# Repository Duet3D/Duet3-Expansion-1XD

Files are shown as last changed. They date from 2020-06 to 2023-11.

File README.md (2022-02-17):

# Duet 3 Expansion 1XD
Hardware information for the Duet 3 Expansion 1XD. This is a CAN-FD connected expansion board for the [Duet 3 Mainboard](https://www.duet3d.com/Duet3Mainboard6HC) and [Duet 3 Mini 5+](https://www.duet3d.com/Duet3Mini5plus) that allows connection for a single external stepper driver and associated peripherals.

Image of Duet 3 Expansion 1XD

Product page is here: https://www.duet3d.com/Duet3Expansion1XD 

Documentation is here: https://docs.duet3d.com/Duet3D_hardware/Duet_3_family/Duet_3_Expansion_1XD

As always please discuss this on the Duet3d forum: https://forum.duet3d.com/

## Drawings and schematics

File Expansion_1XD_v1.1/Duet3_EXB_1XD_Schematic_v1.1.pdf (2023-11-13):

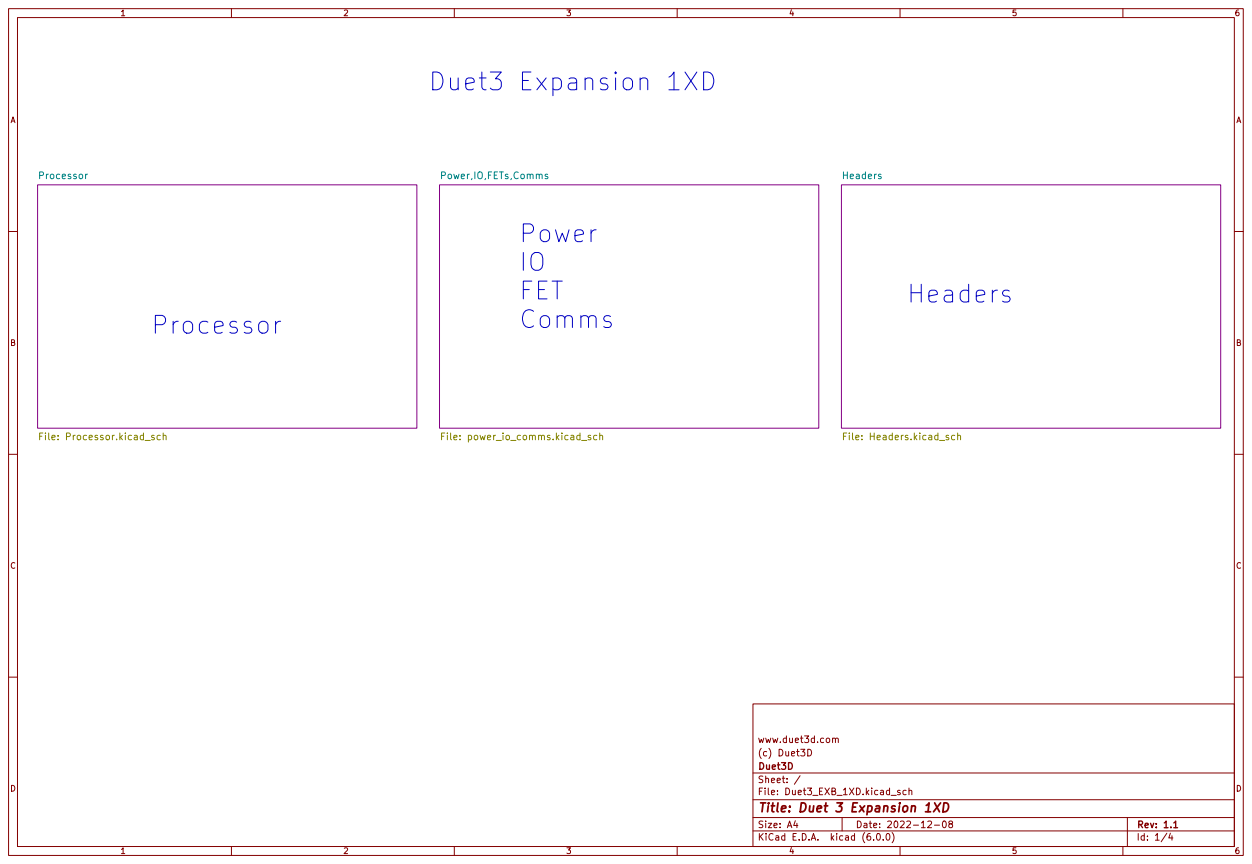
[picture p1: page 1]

Headers File: Headers.kicad_sch Processor File: Processor.kicad_sch

Id: 1/4 Title: Duet 3 Expansion 1XD

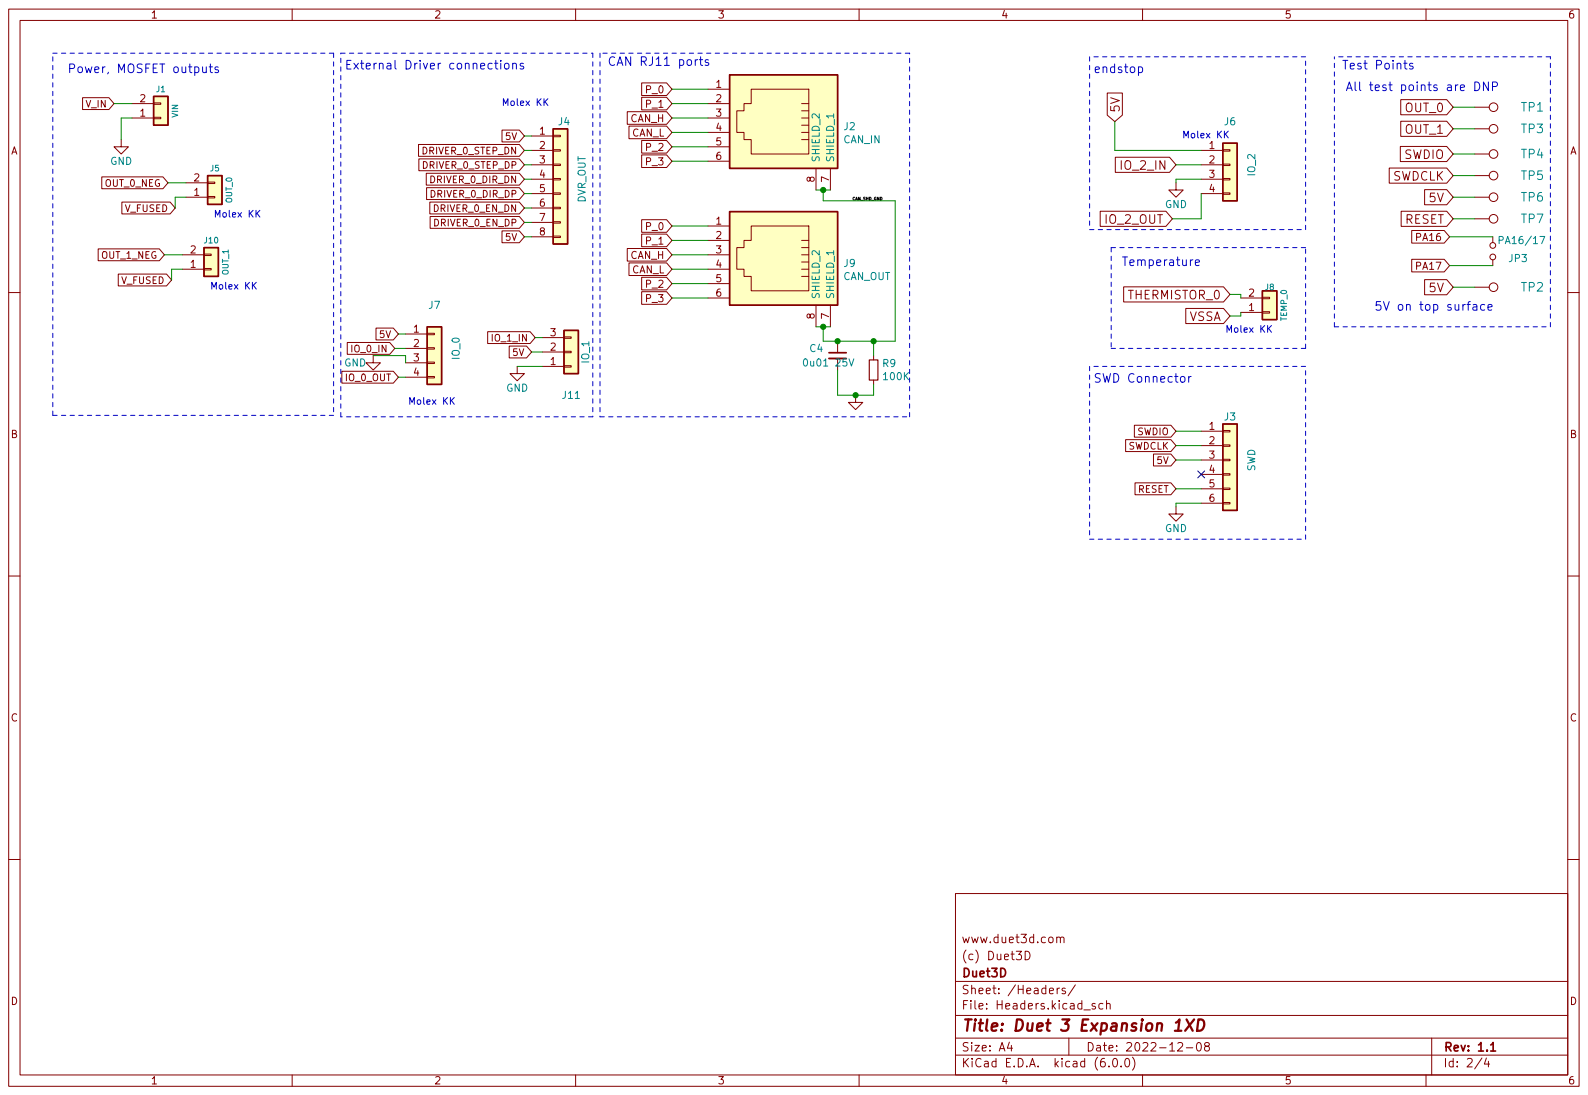
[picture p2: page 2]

All test points are DNP

www.duet3d.com
(c) Duet3D
File: Headers.kicad_sch Sheet: /Headers/ Duet3D

Id: 2/4 Title: Duet 3 Expansion 1XD

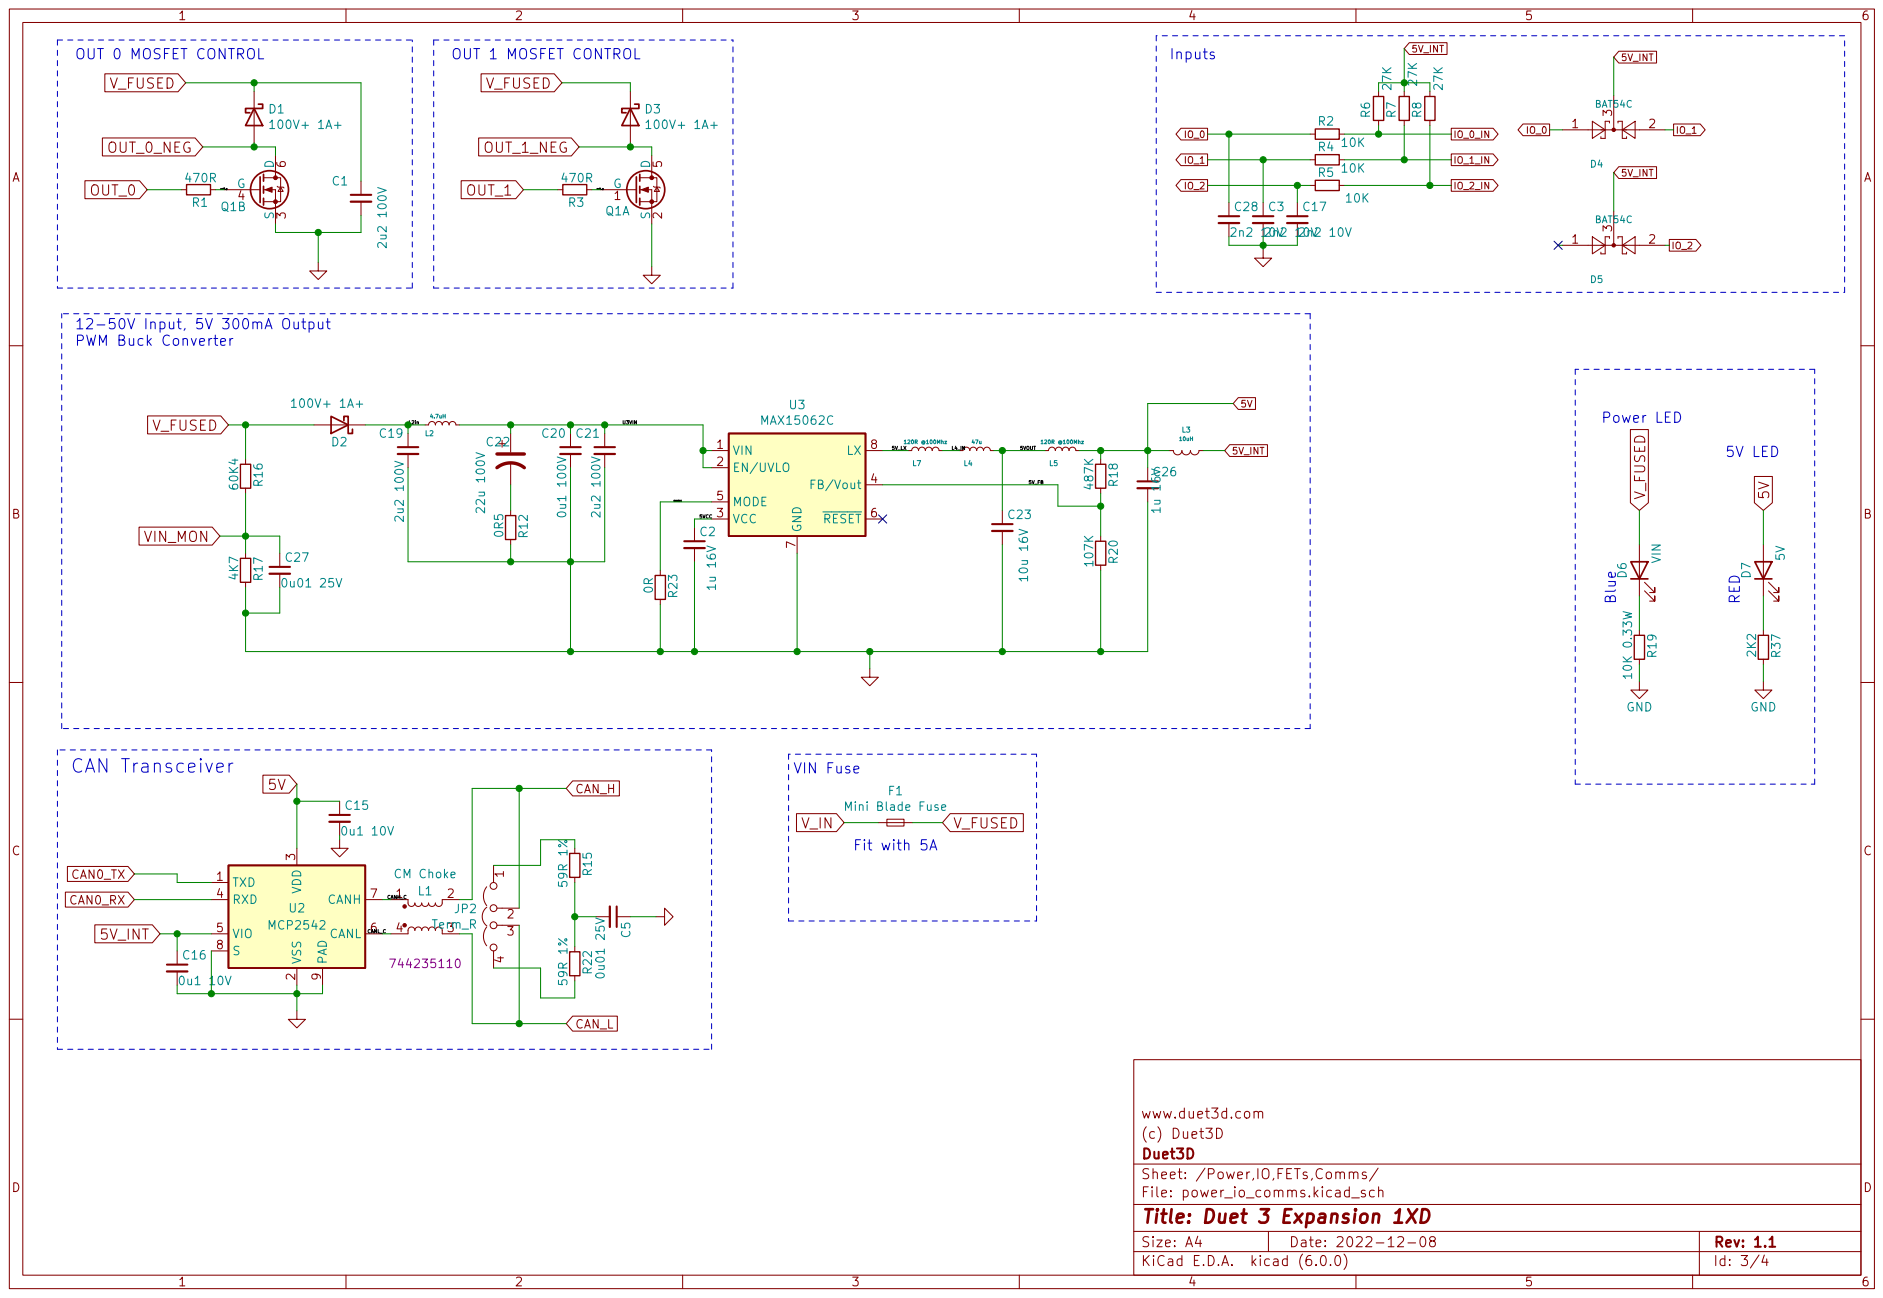
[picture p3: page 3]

Inputs VIN Fuse OUT 0 MOSFET CONTROL
V_FUSED

Fit with 5A CAN Transceiver

3 RXD 4 VIO 5 CANL 6 CANH 7 S

www.duet3d.com
(c) Duet3D
Sheet: /Power,IO,FETs,Comms/ Duet3D

File: power_io_comms.kicad_sch
Id: 3/4 Title: Duet 3 Expansion 1XD

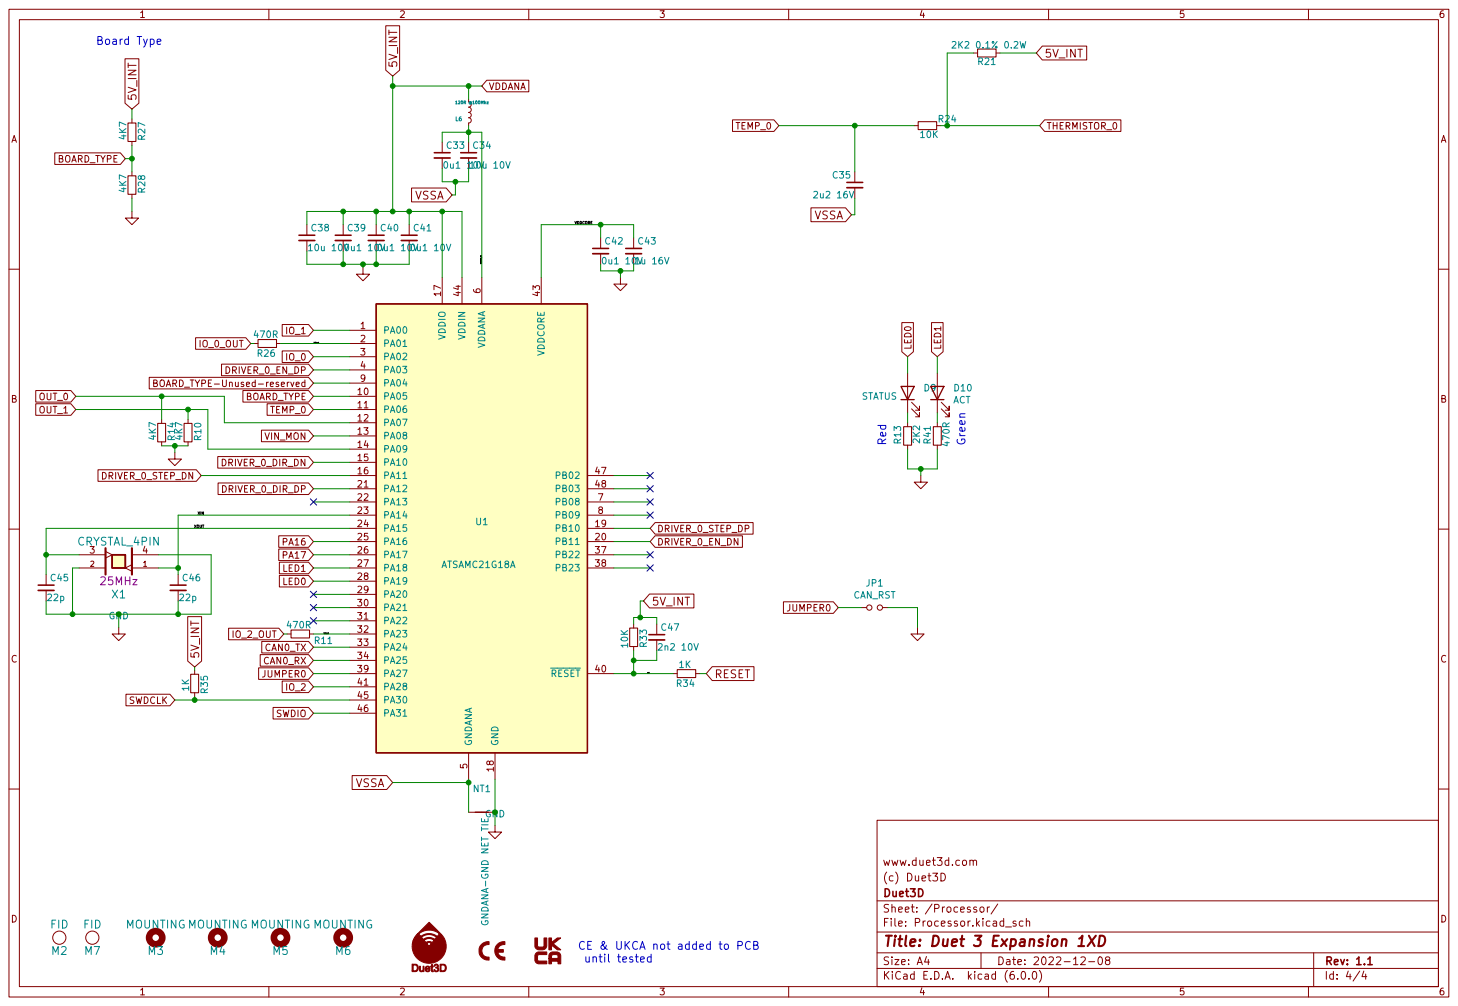
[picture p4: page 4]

www.duet3d.com
(c) Duet3D
File: Processor.kicad_sch Sheet: /Processor/ Duet3D

CE & UKCA not added to PCB
until tested

Id: 4/4 Title: Duet 3 Expansion 1XD

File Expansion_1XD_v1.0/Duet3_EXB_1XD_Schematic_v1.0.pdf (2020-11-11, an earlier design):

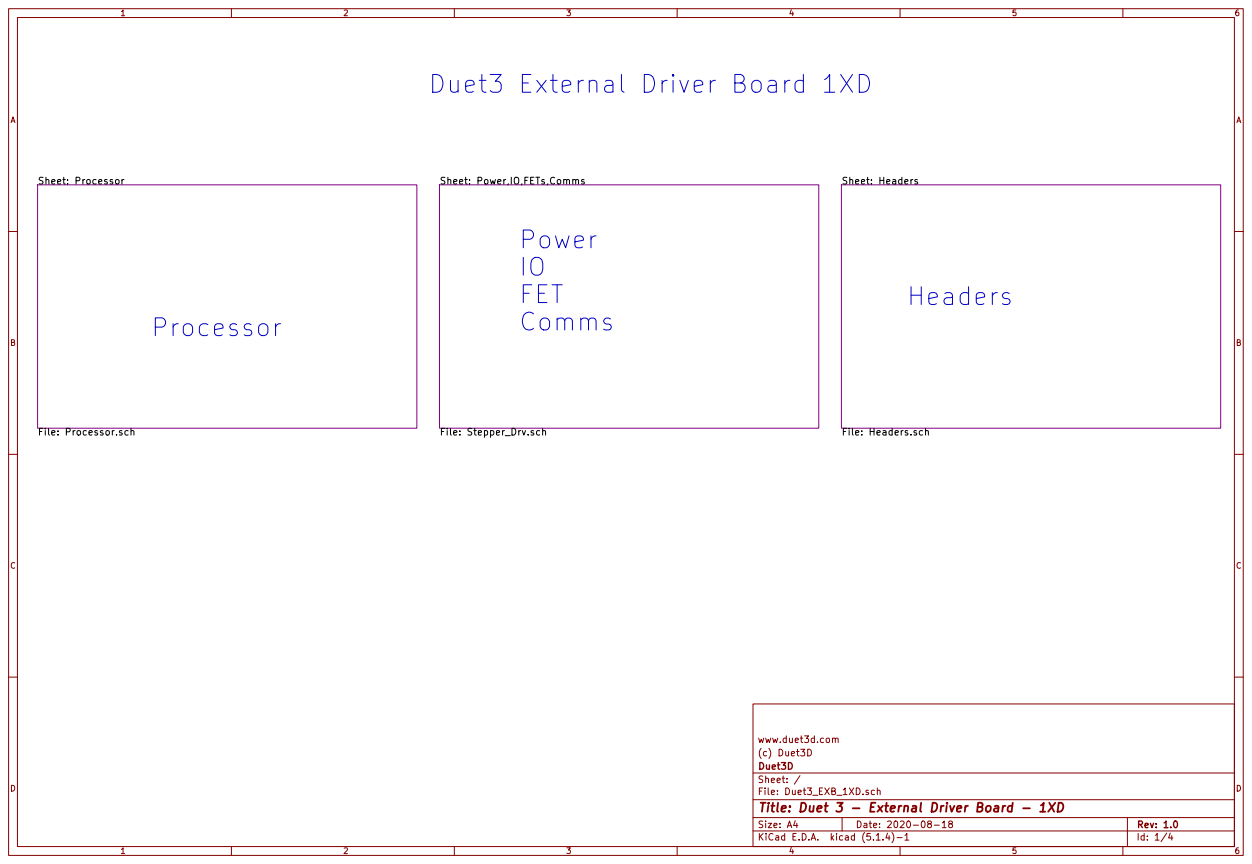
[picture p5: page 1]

Id: 1/4 Title: Duet 3 - External Driver Board - 1XD

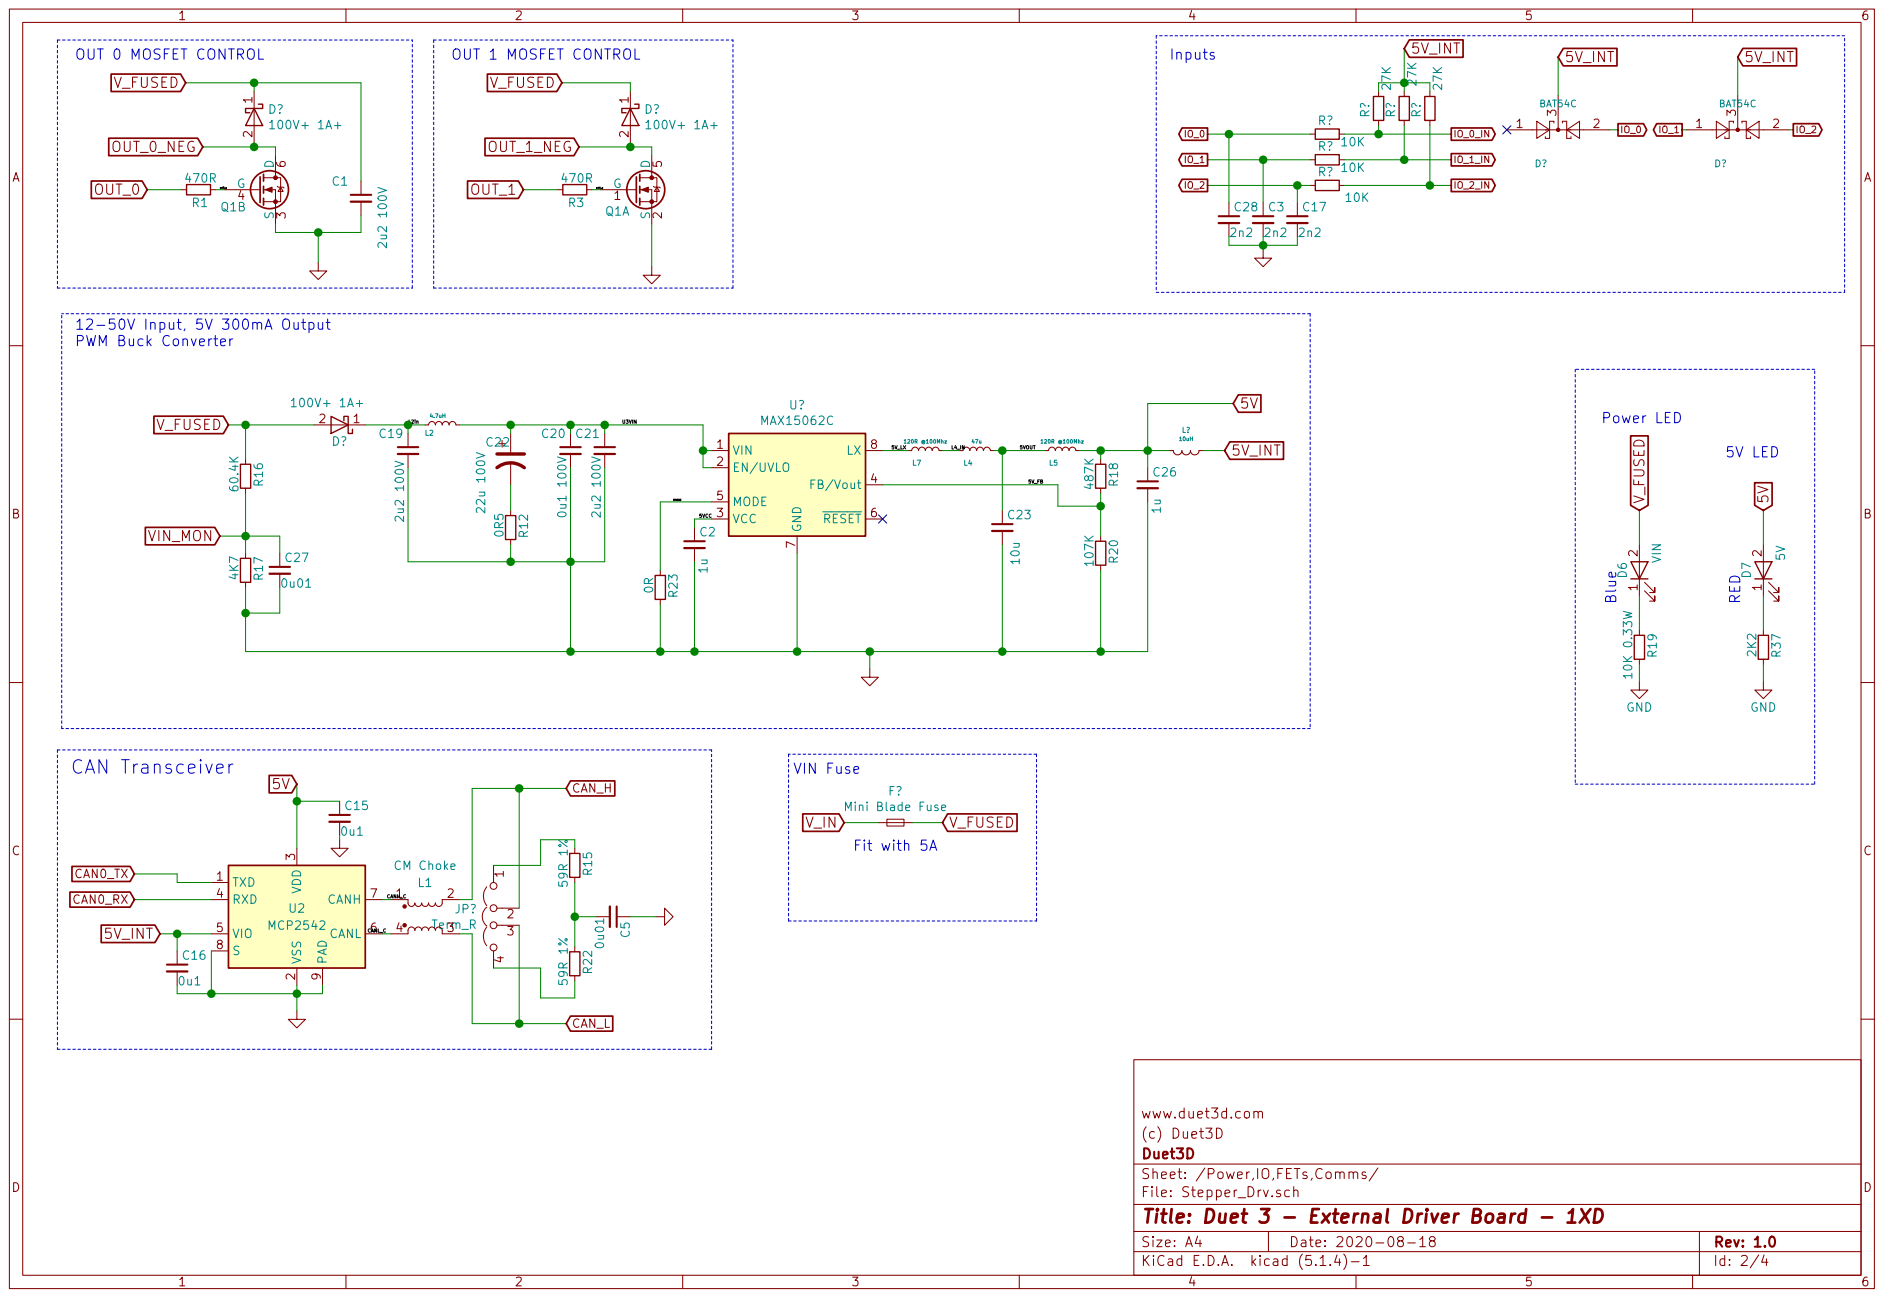
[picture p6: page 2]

3 RXD 4 VIO 5 CANL 6 CANH 7 S

www.duet3d.com
(c) Duet3D
Sheet: /Power,IO,FETs,Comms/ Duet3D

File: Stepper_Drv.sch
Id: 2/4 Title: Duet 3 - External Driver Board - 1XD

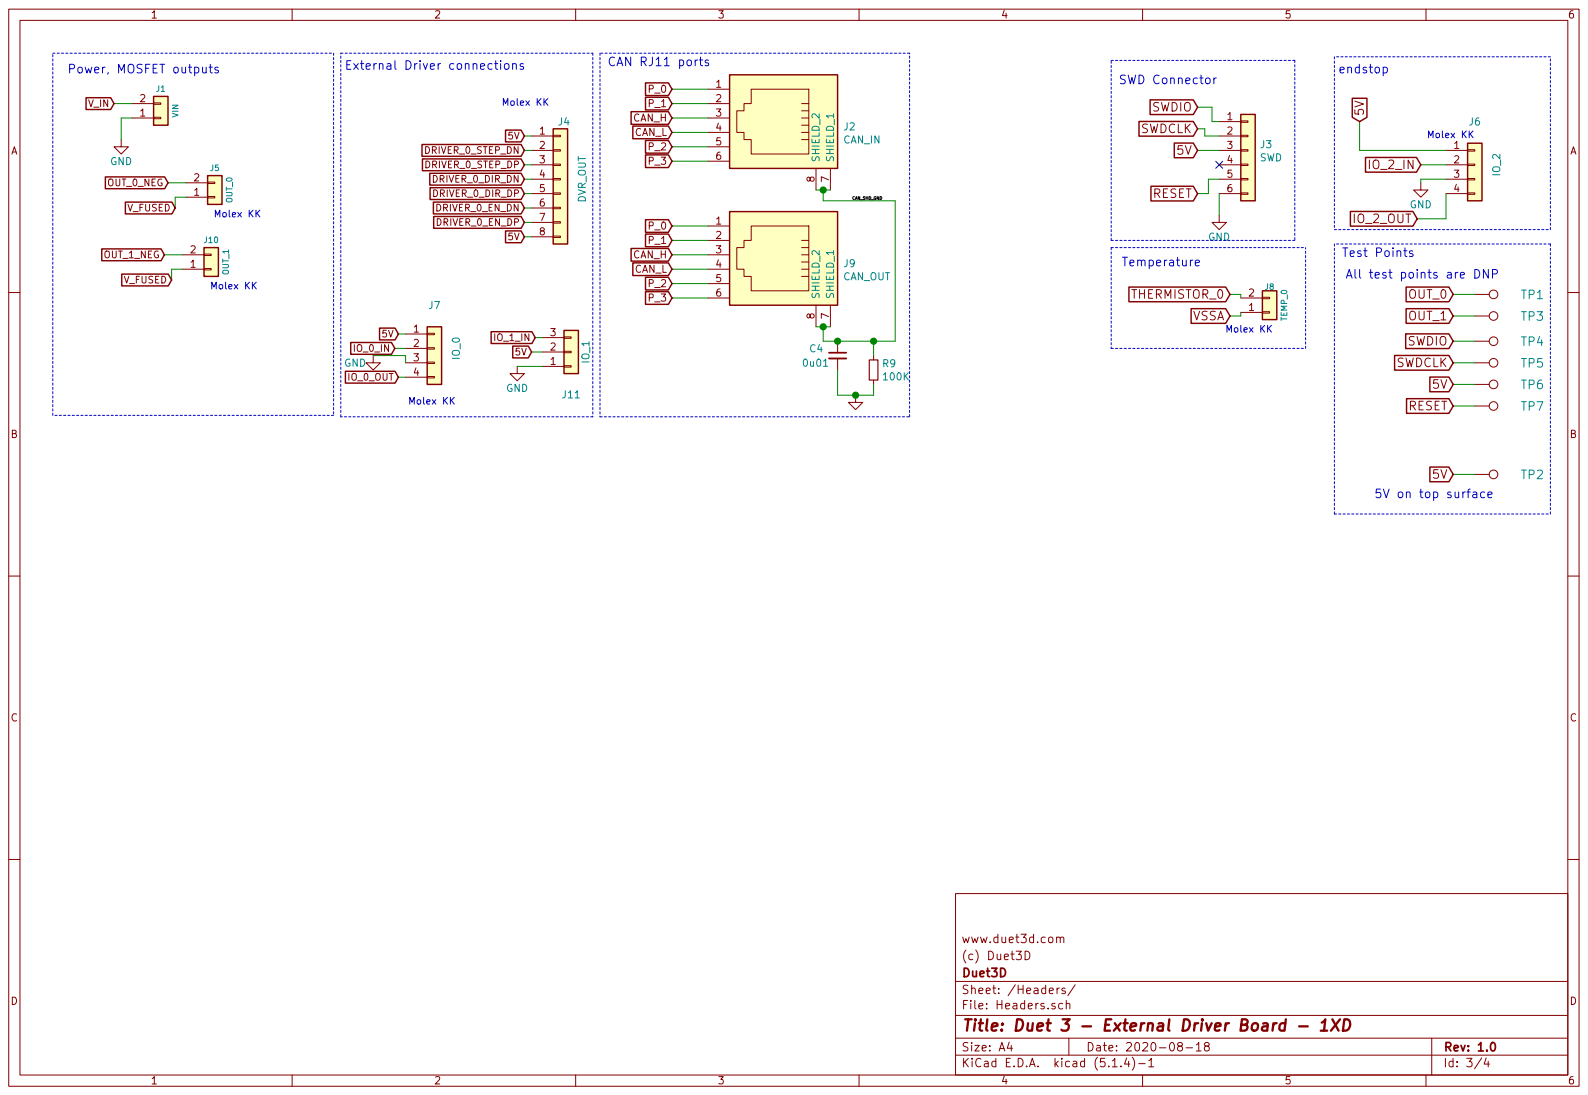
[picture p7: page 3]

www.duet3d.com
(c) Duet3D
File: Headers.sch Sheet: /Headers/ Duet3D

Id: 3/4 Title: Duet 3 - External Driver Board - 1XD

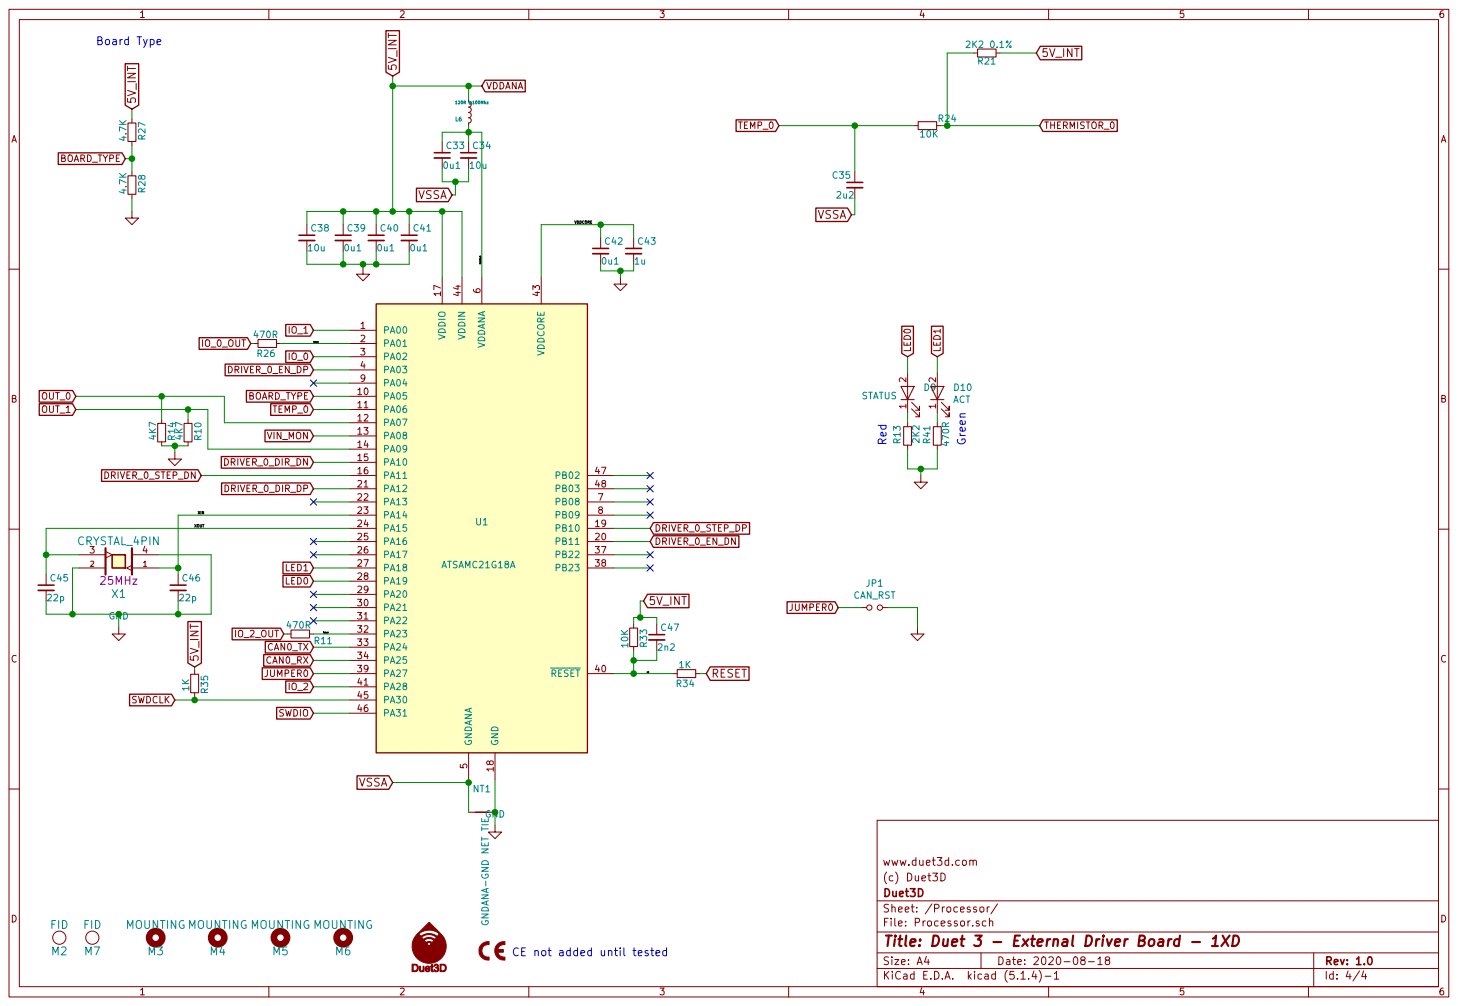
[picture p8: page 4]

rst XIN Board Type

1 2 D10 ACT PA00 1 PA05 10 PA06 11 PA07 12 PA08 13 PA09 14 PA10 15 PA11 16 VDDIO 17 GND 18 PB10 19 PA01 2 PB11 20 PA12 21 PA13 22 PA14 23 PA15 24 PA16 25 PA17 26 PA18 27 PA19 28 PA20 29 PA02 3 PA21 30 PA22 31 PA23 32 PA24 33 PA25 34 PB22 37 PB23 38 PA27 39 PA03 4 RESET 40 PA28 41 VDDCORE 43 VDDIN 44 PA30 45 PA31 46 PB02 47 PB03 48 GNDANA
LED1 BOARD_TYPE
TEMP_0

NT1GNDANA-GND NET TIE GND GND

(c) Duet3D
File: Processor.sch Sheet: /Processor/ Duet3D

Id: 4/4 Title: Duet 3 - External Driver Board - 1XD

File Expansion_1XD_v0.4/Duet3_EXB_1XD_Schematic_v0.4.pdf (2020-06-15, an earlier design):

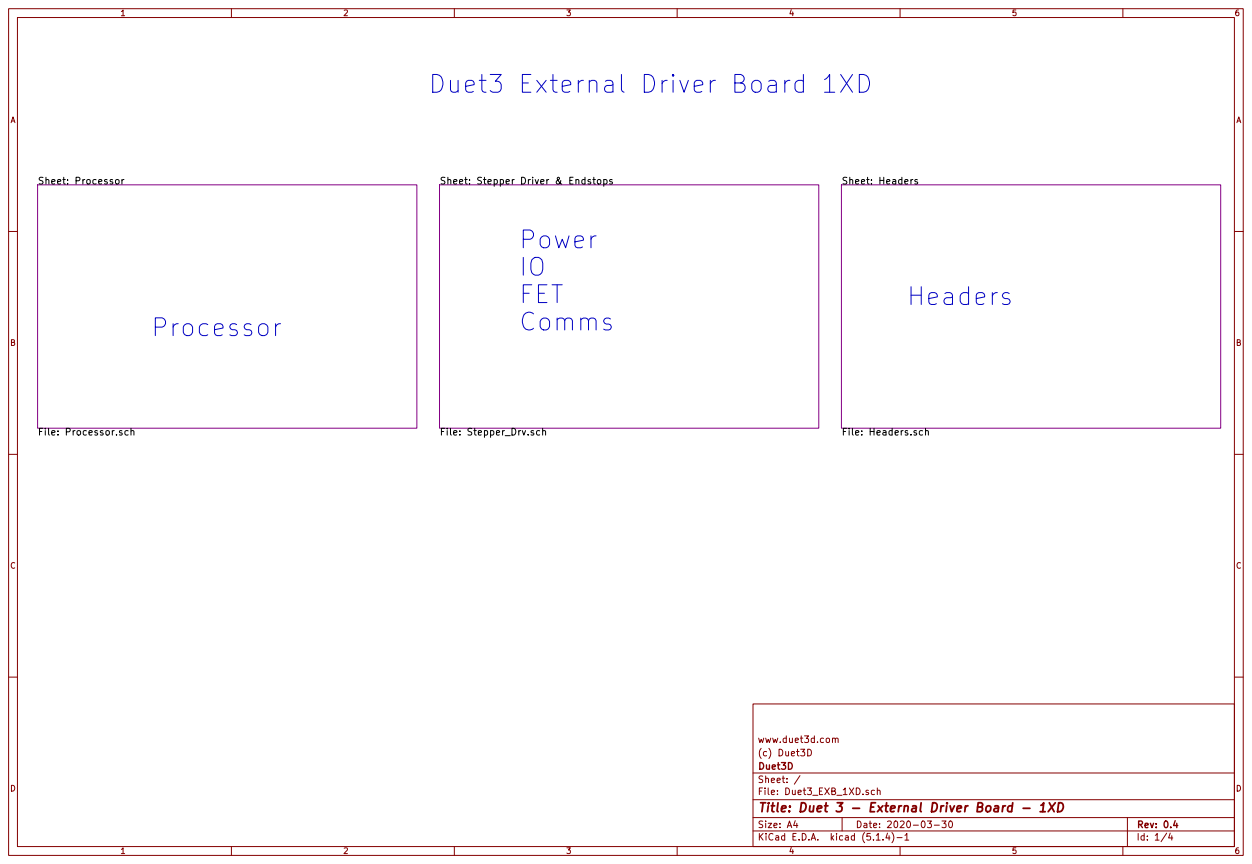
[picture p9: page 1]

Id: 1/4 Title: Duet 3 - External Driver Board - 1XD

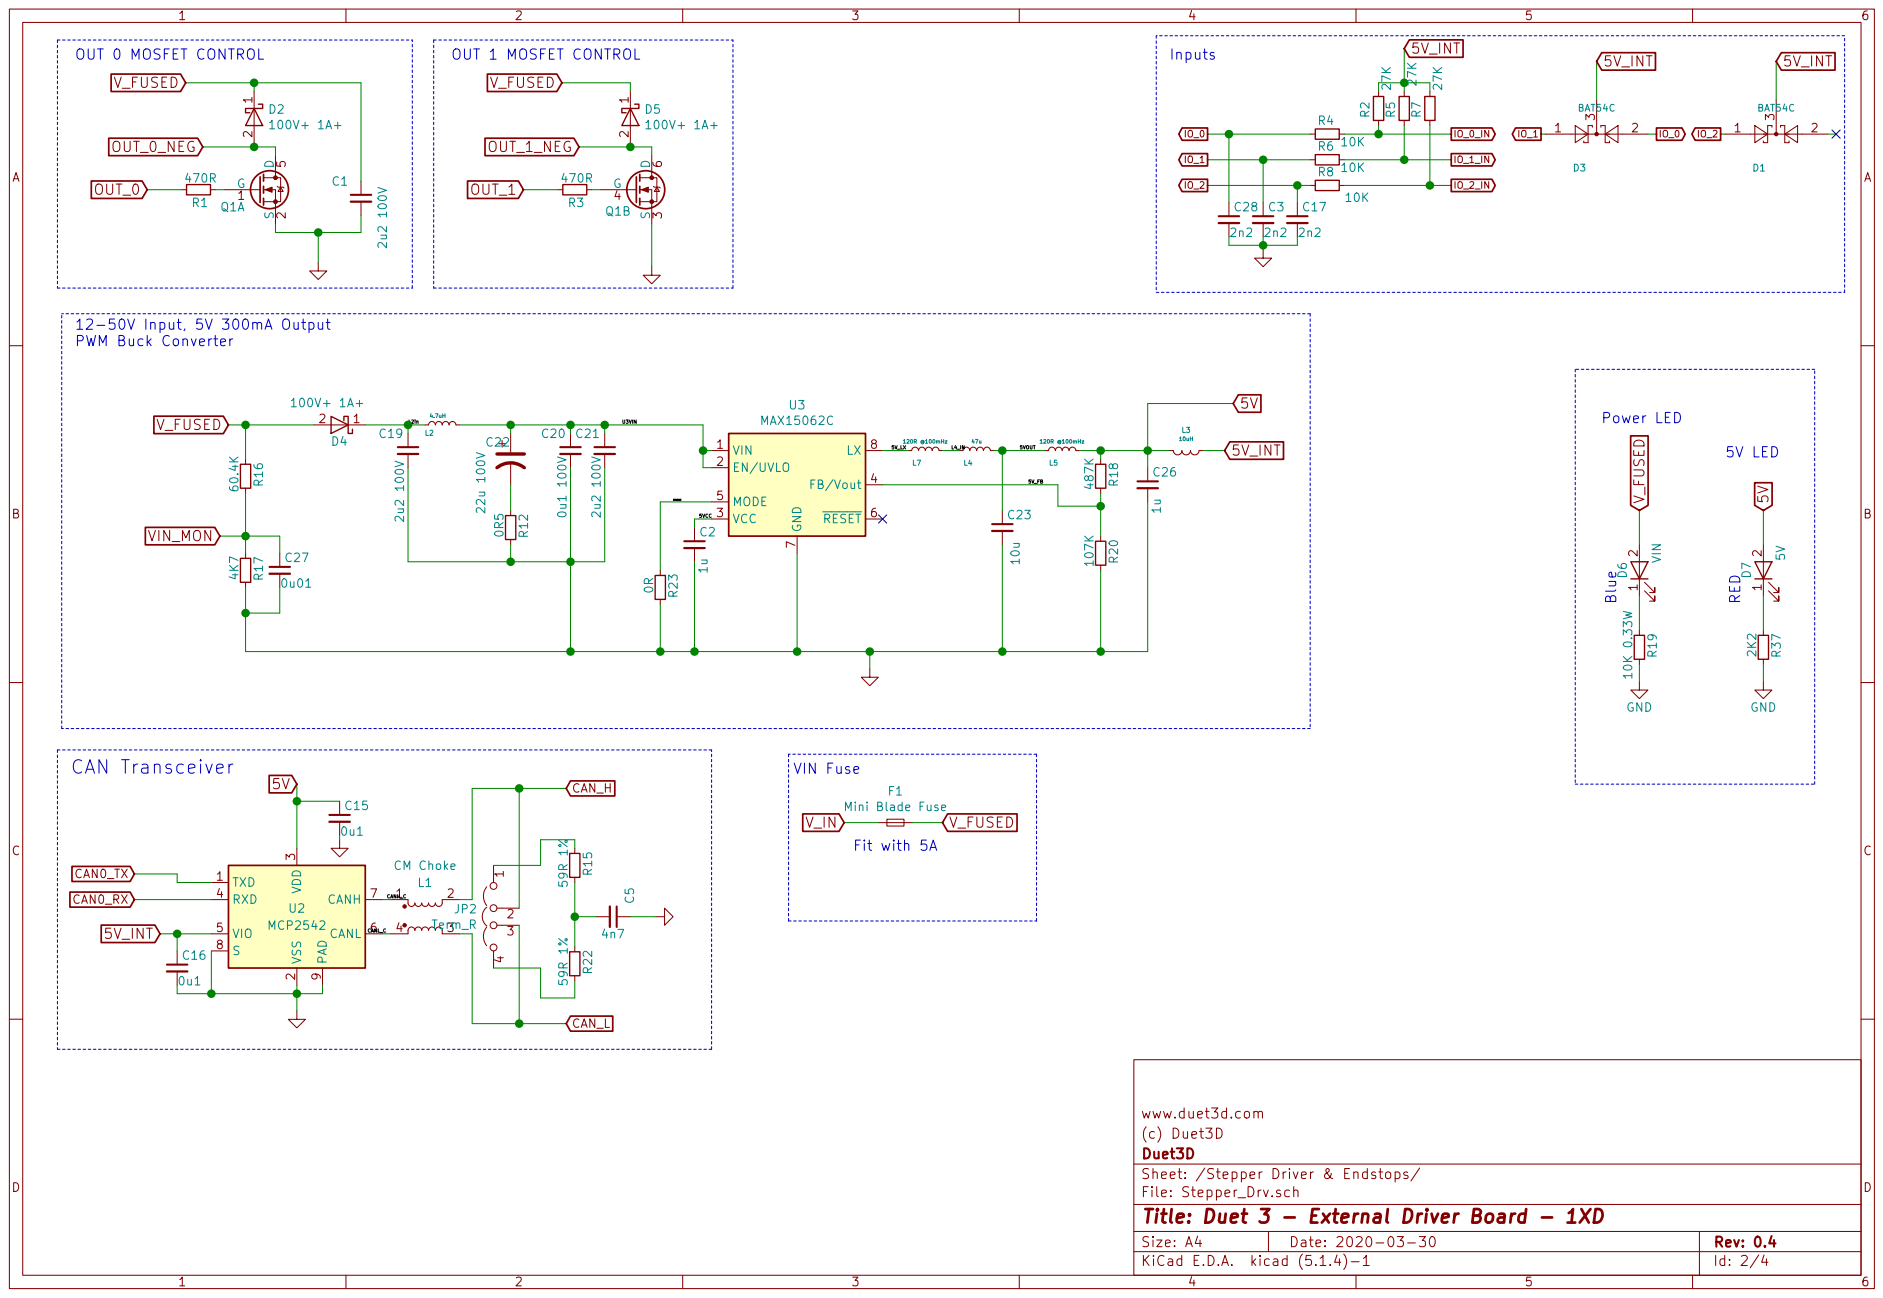
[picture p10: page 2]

V_FUSED OUT_1_NEG

3 RXD 4 VIO 5 CANL 6 CANH 7 S

www.duet3d.com
(c) Duet3D
Sheet: /Stepper Driver & Endstops/ Duet3D

File: Stepper_Drv.sch
Id: 2/4 Title: Duet 3 - External Driver Board - 1XD

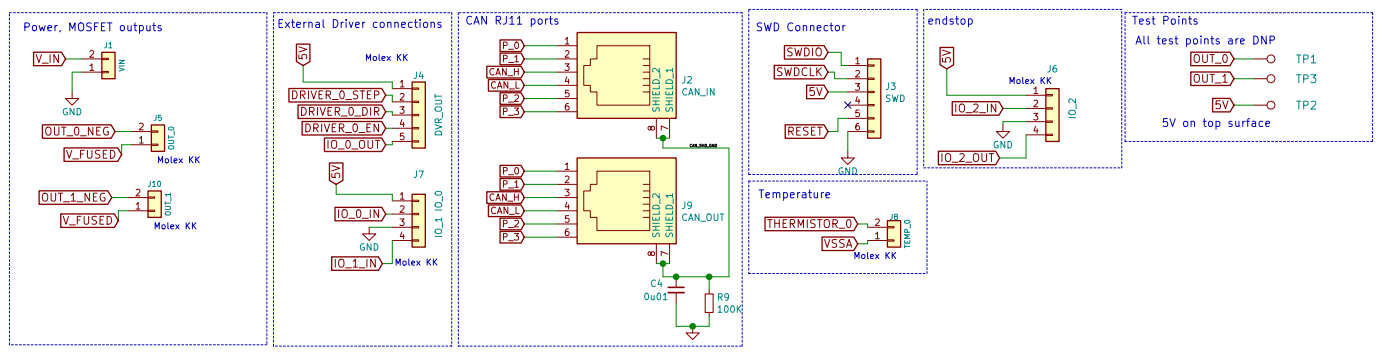
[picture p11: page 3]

www.duet3d.com
(c) Duet3D
File: Headers.sch Sheet: /Headers/ Duet3D

Id: 3/4 Title: Duet 3 - External Driver Board - 1XD

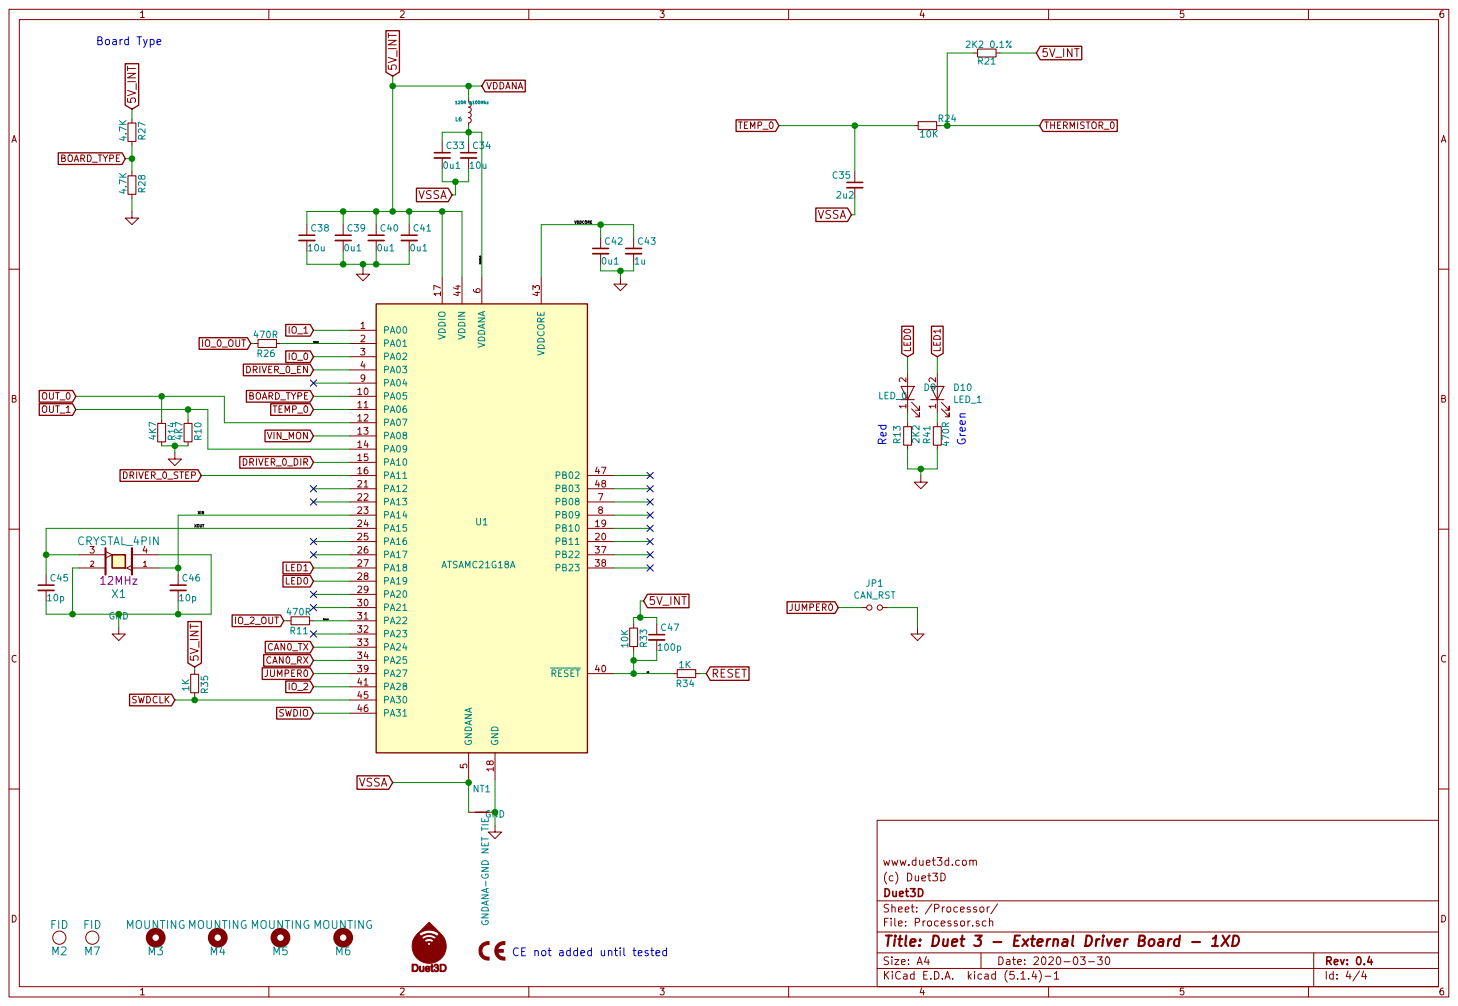
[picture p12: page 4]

(c) Duet3D
File: Processor.sch Sheet: /Processor/ Duet3D

Id: 4/4 Title: Duet 3 - External Driver Board - 1XD

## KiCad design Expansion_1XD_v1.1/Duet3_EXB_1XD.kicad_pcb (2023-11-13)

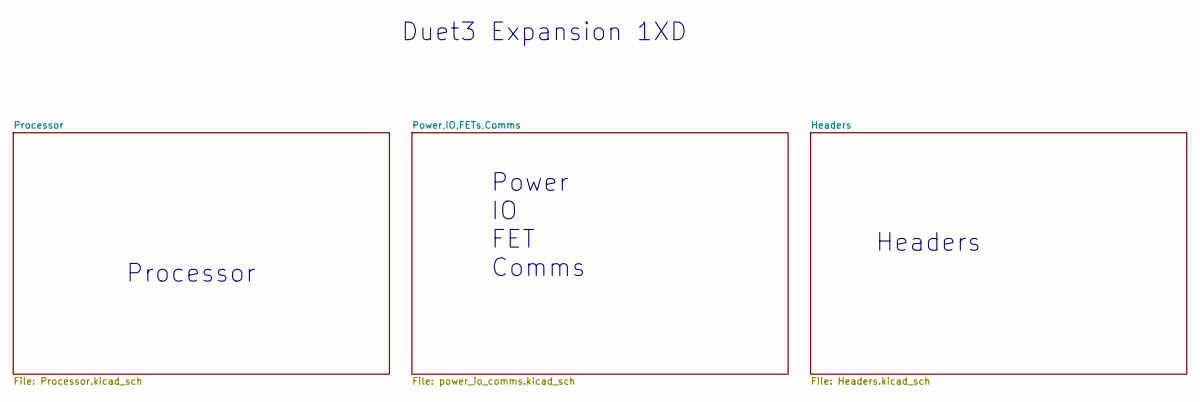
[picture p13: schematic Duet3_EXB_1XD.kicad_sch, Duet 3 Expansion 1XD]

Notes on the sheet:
Duet3 Expansion 1XD
Processor
Power IO FET Comms
Headers

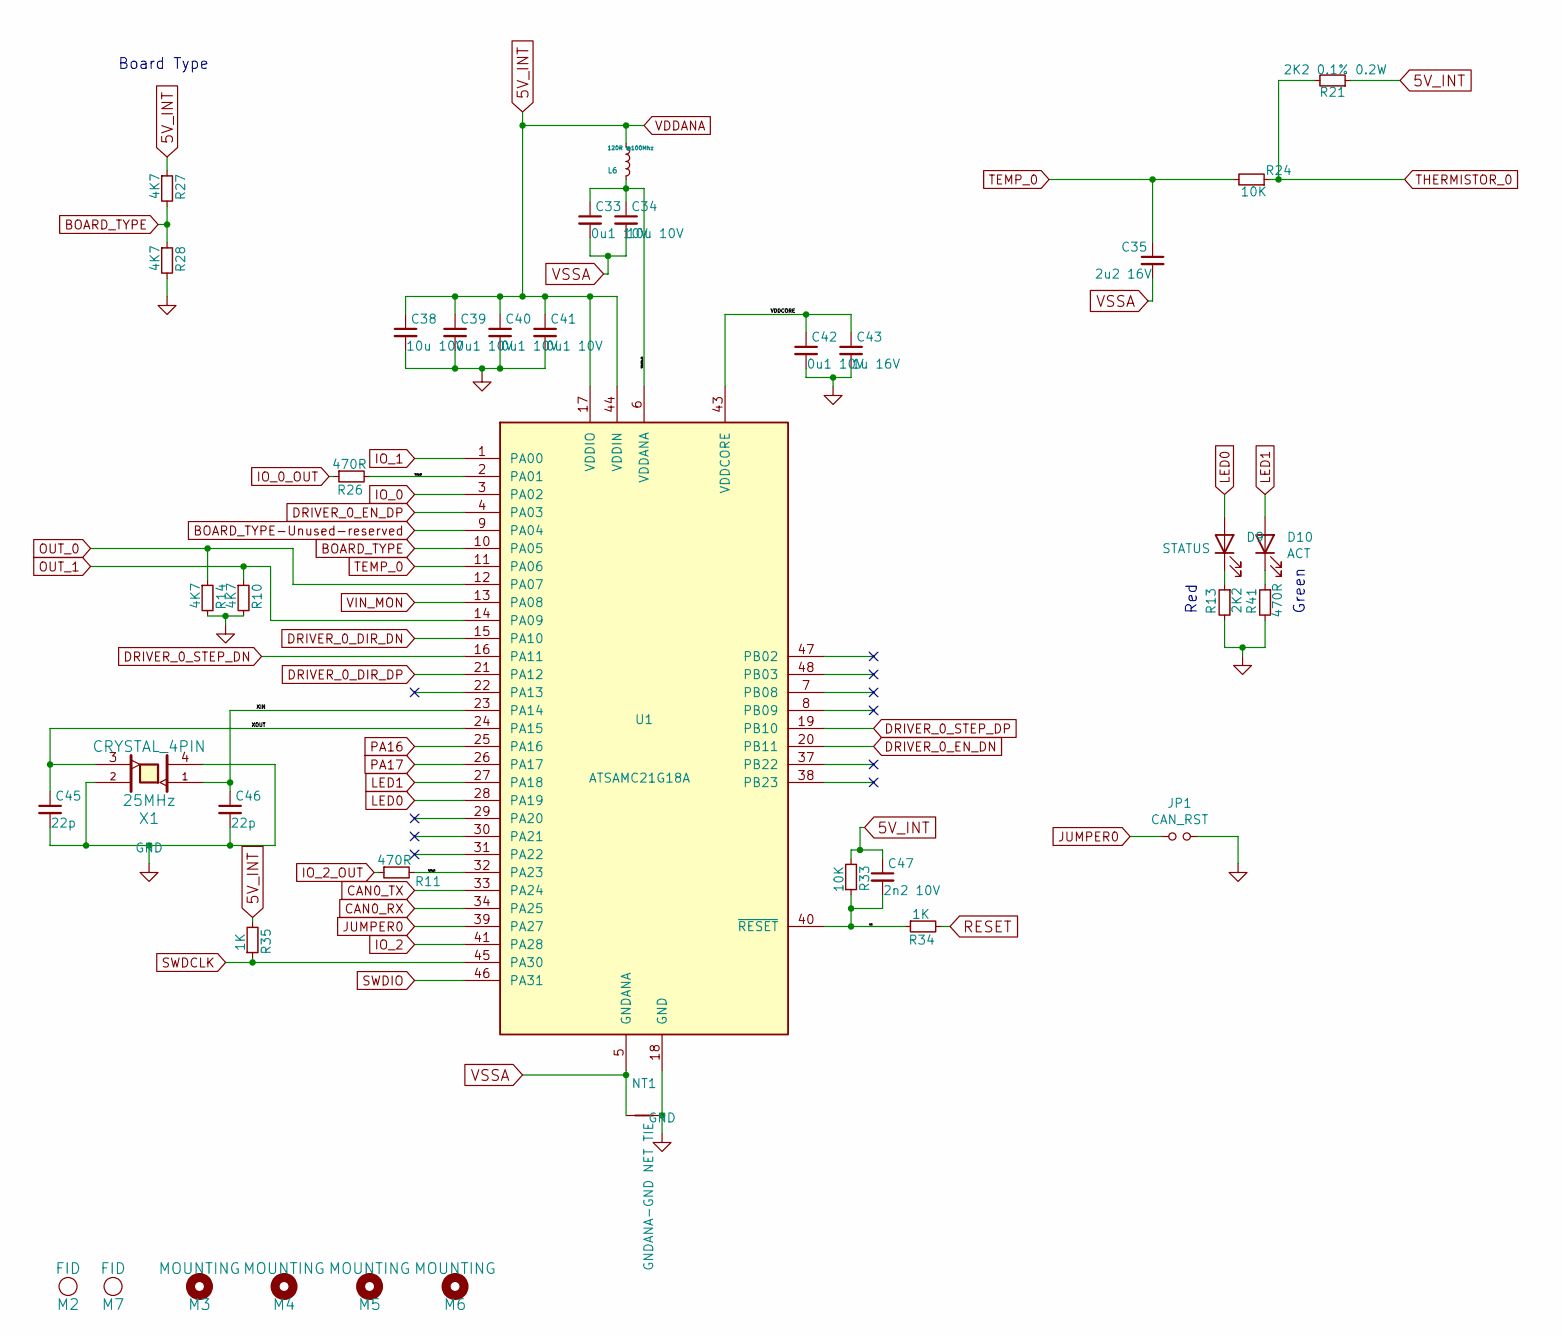
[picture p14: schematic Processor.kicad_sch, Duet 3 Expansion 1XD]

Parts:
C33, C39, C40, C41, C42: 0u1 10V; C_0402_1005Metric_Wbry; Part Number CL05B104KP5NNNC
C34, C38: 10u 10V; C_0805_2012Metric; Part Number GRM21BR71A106KA73K
C35: 2u2 16V; C_0402_1005Metric_Wbry; Part Number GRM155C81C225ME15D
C43: 1u 16V; C_0603_1608Metric_Wbry; Part Number CL10B105KO8NNNC
C45, C46: 22p; C_0402_1005Metric_Wbry; Part Number C0402C220J4GACTU
C47: 2n2 10V; C_0402_1005Metric_Wbry; Part Number 0402YC222KAT2A
D9: STATUS; LED_0603_1608Metric; Part Number 150060RS75000 or equivalent Red
D10: ACT; LED_0603_1608Metric; Part Number 150060VS75000 or equivalent Green
JP1: CAN_RST; PinHeader_1x02_P2.54mm_Vertical; Part Number 2 way pin header + Jumper
L6: 120R @100Mhz; L_0402_1005Metric; Part Number 7427927311 or similar
M2, M7: FID; Fiducial_1mm_Mask2mm; Part Number virtual component - DNP
M3, M4, M5, M6: MOUNTING; MountingHole_3.2mm_M3; Part Number virtual component - DNP
NT1: GNDANA-GND NET TIE; NetTie-2_SMD_Pad0.5mm; Part Number virtual component - DNP
R10, R14, R27, R28: 4K7; R_0402_1005Metric_Wbry; Part Number RK73H1ETTP4701F
R11, R26, R41: 470R; R_0402_1005Metric_Wbry; Part Number RK73H1ETTP4700F
R13: 2K2; R_0402_1005Metric_Wbry; Part Number RK73H1ETTP2201F
R21: 2K2 0.1% 0.2W; R_0603_1608Metric_Wbry; Part Number ERJ-PB3B2201V
R24, R33: 10K; R_0402_1005Metric_Wbry; Part Number RK73H1ETTP1002F
R34, R35: 1K; R_0402_1005Metric_Wbry; Part Number RK73H1ETTP1001F
U1: ATSAMC21G18A; QFN-48-1EP_7x7mm_P0.5mm_EP5.2x5.2mm_ThermalVias; Part Number ATSAMC21G18A-MU
X1: CRYSTAL_4PIN; Crystal_SMD_ECS-33B-4Pin_3.2x2.5mm; Part Number TSX-3225 25.0000MF10P

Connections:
5V_INT: C38.1, C39.1, C40.1, C41.1, C47.1, L6.1, R21.1, R27.1, R33.2, R35.2, U1.17 (VDDIO), U1.36 (VDDIO), U1.44 (VDDIN); also elsewhere on the board
/Processor/VDDANA_IN: C33.1, C34.1, L6.2, U1.6 (VDDANA)
/Processor/VDDCORE: C42.1, C43.1, U1.43 (VDDCORE)
/Processor/XIN: C46.1, U1.23 (PA14), X1.1
/Processor/XOUT: C45.1, U1.24 (PA15), X1.3
/Processor/io0out: R26.2, U1.2 (PA01)
/Processor/io2out: R11.2, U1.32 (PA23)
/Processor/rst: C47.2, R33.1, R34.1, U1.40 (~RESET)
BOARD_TYPE: R27.2, R28.1, U1.10 (PA05)
BOARD_TYPE-Unused-reserved: U1.9 (PA04)
CAN0_RX: U1.34 (PA25); also elsewhere on the board
CAN0_TX: U1.33 (PA24); also elsewhere on the board
DRIVER_0_DIR_DN: U1.15 (PA10); also elsewhere on the board
DRIVER_0_DIR_DP: U1.21 (PA12); also elsewhere on the board
DRIVER_0_EN_DN: U1.20 (PB11); also elsewhere on the board
DRIVER_0_EN_DP: U1.4 (PA03); also elsewhere on the board
DRIVER_0_STEP_DN: U1.16 (PA11); also elsewhere on the board
DRIVER_0_STEP_DP: U1.19 (PB10); also elsewhere on the board
GND: C38.2, C39.2, C40.2, C41.2, C42.2, C43.2, C45.2, C46.2, JP1.2, NT1.2, R10.2, R13.2, R14.2, R28.2, R41.2, U1.18 (GND), U1.35 (GND), U1.42 (GND), U1.49 (GND), X1.2, X1.4; also elsewhere on the board
IO_0: U1.3 (PA02); also elsewhere on the board
IO_0_OUT: R26.1; also elsewhere on the board
IO_1: U1.1 (PA00); also elsewhere on the board
IO_2: U1.41 (PA28); also elsewhere on the board
IO_2_OUT: R11.1; also elsewhere on the board
JUMPER0: JP1.1, U1.39 (PA27)
LED0: D9.2 (A), U1.28 (PA19)
LED1: D10.2 (A), U1.27 (PA18)
unnamed: D9.1 (K), R13.1
unnamed: D10.1 (K), R41.1
OUT_0: R14.1, U1.12 (PA07); also elsewhere on the board
OUT_1: R10.1, U1.14 (PA09); also elsewhere on the board
PA16: U1.25 (PA16); also elsewhere on the board
PA17: U1.26 (PA17); also elsewhere on the board
RESET: R34.2; also elsewhere on the board
SWDCLK: R35.1, U1.45 (PA30); also elsewhere on the board
SWDIO: U1.46 (PA31); also elsewhere on the board
TEMP_0: C35.1, R24.2, U1.11 (PA06)
THERMISTOR_0: R21.2, R24.1; also elsewhere on the board
VIN_MON: U1.13 (PA08); also elsewhere on the board
VSSA: C33.2, C34.2, C35.2, NT1.1, U1.5 (GNDANA); also elsewhere on the board

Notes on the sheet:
Board Type
Green
Red

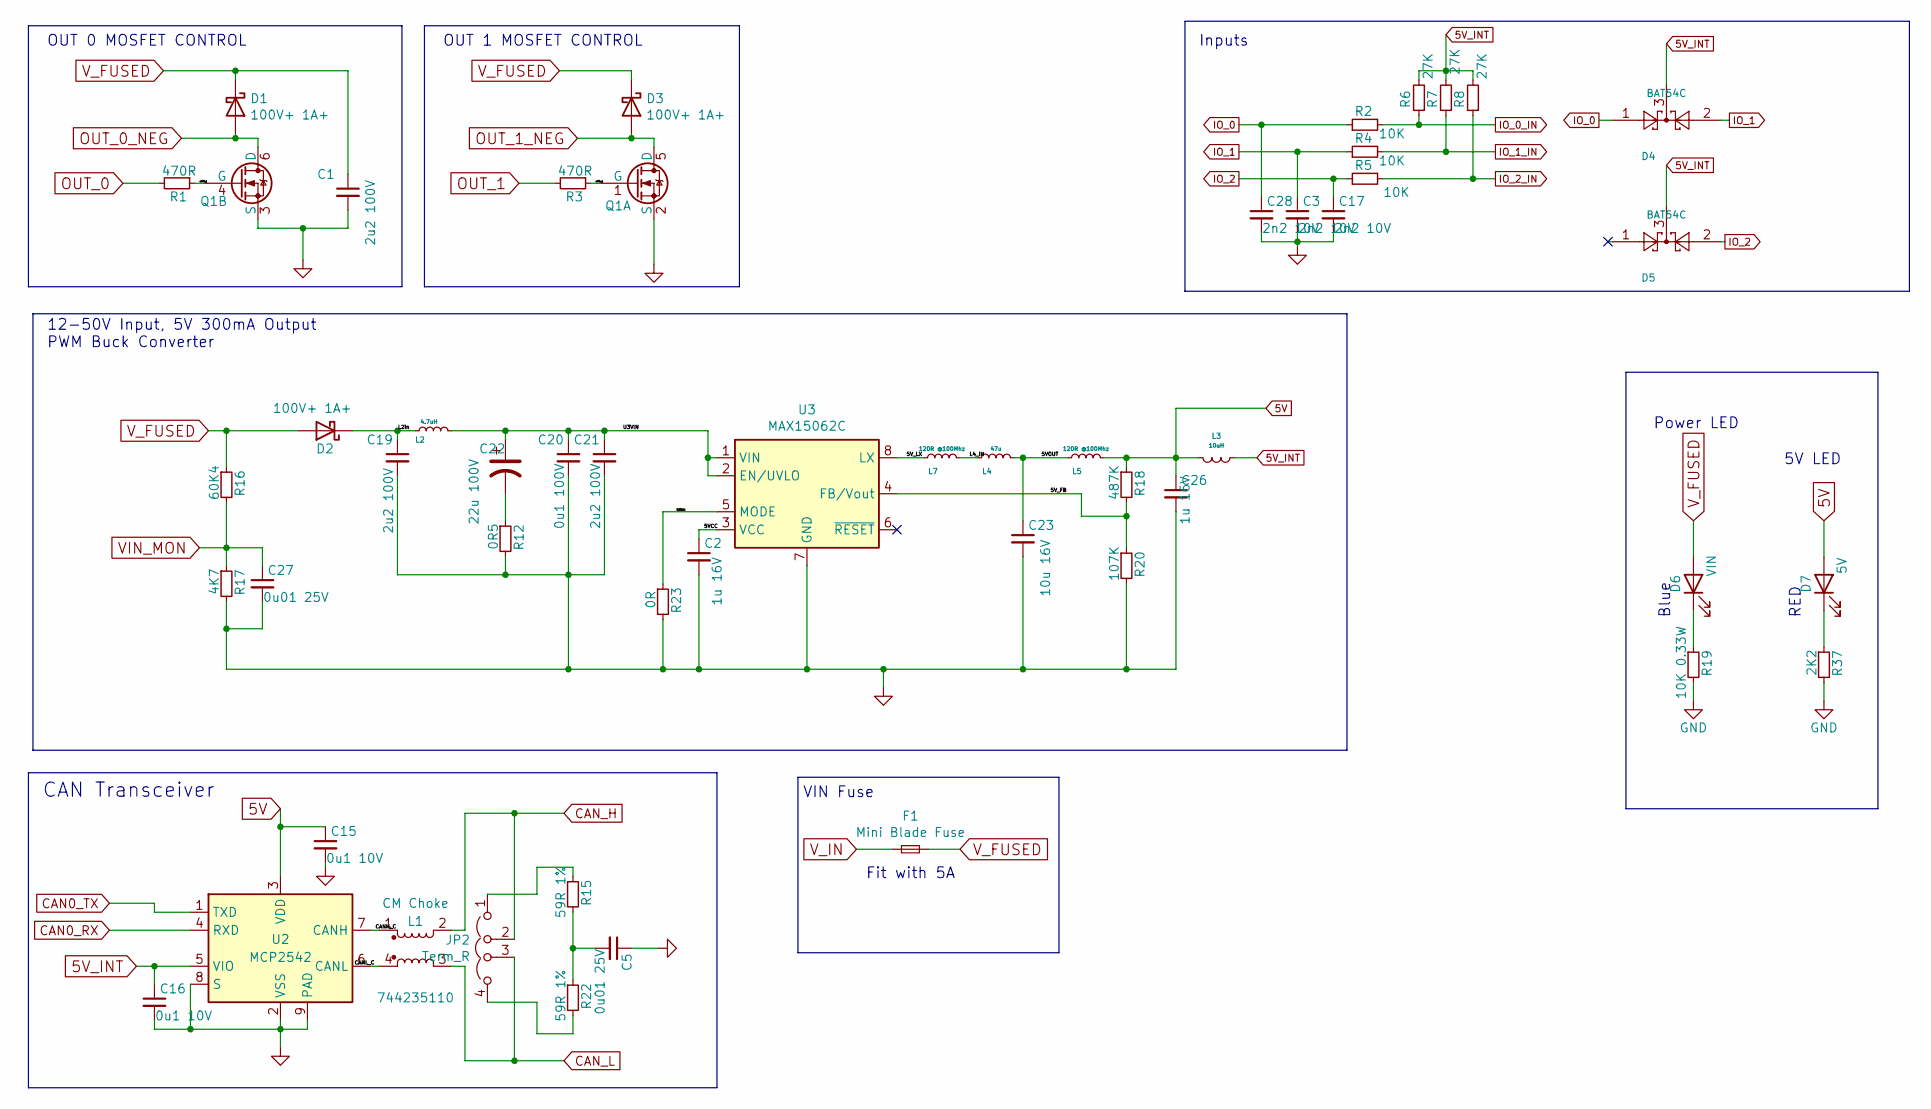
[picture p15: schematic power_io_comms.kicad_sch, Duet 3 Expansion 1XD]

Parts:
C1, C19, C21: 2u2 100V; C_1210_3225Metric; Part Number CL32B225KCJSNNE
C2: 1u 16V; C_0603_1608Metric_Wbry; Rating 35V +; Part Number CL10B105KO8NNNC
C3, C17, C28: 2n2 10V; C_0402_1005Metric_Wbry; Part Number 0402YC222KAT2A
C5, C27: 0u01 25V; C_0402_1005Metric_Wbry; Part Number TMK105B7103KV-F
C15, C16: 0u1 10V; C_0402_1005Metric_Wbry; Part Number CL05B104KP5NNNC
C20: 0u1 100V; C_0603_1608Metric_Wbry; Part Number CL10B104KC8NNNC
C22: 22u 100V; CP_Elec_8x10; Part Number EEE-2AA220UP or similar
C23: 10u 16V; C_1206_3216Metric; Rating 6.3V or higher, similar X7R; Part Number CL31B106MOHNNNE
C26: 1u 16V; C_0603_1608Metric_Wbry; Rating 10V+; Part Number CL10B105KO8NNNC
D1, D2, D3: 100V+ 1A+; D_SMF; Part Number SS1FH10-M3/H or similar
D4, D5: BAT54C; SOT-23; Part Number BAT54CLT1G
D6: VIN; LED_0603_1608Metric; Part Number 150060BS75000 or equiv Blue
D7: 5V; LED_0603_1608Metric; Part Number 150060RS75000 or equivalent Red
F1: Mini Blade Fuse; MCCQ-122-minibladefuseholder; Part Number Fit with 5A Fuse
JP2: Term_R; PinHeader_1x04_P2.54mm_Vertical; Part Number 4 way pin header + 2xJumpers
L1: CM Choke; Wurth_CM_Choke_1812_744235nnn; Part Number 744235110
L2: 4.7uH; L_0805_2012Metric; Part Number MBKK2012T4R7M or CB2012T4R7M or similar
L3: 10uH; L_1008_2512Metric; Part Number e.g. CBC2518T100M
L4: 47u; L_Taiyo-Yuden_NR-40xx; Part Number NRS4018T470MDGJ or similar
L5, L7: 120R @100Mhz; L_0402_1005Metric; Part Number 7427927311 or similar
Q1: Q_DUAL_NMOS; Fairchild_DualPower33-6_3x3mm; Part Number DMT6018LDR-13-ND
R1, R3: 470R; R_0402_1005Metric_Wbry; Part Number RK73H1ETTP4700F
R2, R4, R5: 10K; R_0402_1005Metric_Wbry; Part Number RK73H1ETTP1002F
R6, R7, R8: 27K; R_0402_1005Metric_Wbry; Part Number RK73H1ETTP2702F
R12: 0R5; R_0402_1005Metric_Wbry; Part Number CSR0402FKR500
R15, R22: 59R 1%; R_0402_1005Metric_Wbry; Part Number RK73H1ETTP59R0F
R16: 60K4; R_0402_1005Metric_Wbry; Part Number ERJ-2RKF6042X
R17: 4K7; R_0402_1005Metric_Wbry; Part Number RK73H1ETTP4701F
R18: 487K; R_0402_1005Metric_Wbry; Part Number RK73H1ETTP4873F
R19: 10K 0.33W; R_0805_2012Metric; Part Number CRGH0805F10K
R20: 107K; R_0402_1005Metric_Wbry; Part Number RK73H1ETTP1073F
R23: 0R; R_0402_1005Metric_Wbry; Part Number CR0402-J/-000GLF
R37: 2K2; R_0402_1005Metric_Wbry; Part Number RK73H1ETTP2201F
U2: MCP2542; DFN-8-1EP_3x2mm_P0.5mm_EP1.3x1.5mm; Part Number MCP2542FDT-E/MNY
U3: MAX15062C; DFN-8_2x2mm_P0.5mm; Part Number MAX15062CATA+T

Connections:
5V: C15.1, C26.1, D7.2 (A), L3.1 (A), L5.2, R18.1, U2.3 (VDD); also elsewhere on the board
5V_INT: C16.1, D4.3, D5.3, L3.2 (B), R6.2, R7.2, R8.2, U2.5 (VIO); also elsewhere on the board
/Power,IO,FETs,Comms/5VCC: C2.1, U3.3 (VCC)
/Power,IO,FETs,Comms/5VMODE: R23.1, U3.5 (MODE)
/Power,IO,FETs,Comms/5VOUT: C23.1, L4.2, L5.1
/Power,IO,FETs,Comms/5V_FB: R18.2, R20.1, U3.4 (FB/Vout)
/Power,IO,FETs,Comms/5V_LX: L7.1, U3.8 (LX)
/Power,IO,FETs,Comms/CANH_C: L1.1, U2.7 (CANH)
/Power,IO,FETs,Comms/CANL_C: L1.4, U2.6 (CANL)
/Power,IO,FETs,Comms/L2in: C19.1, D2.1 (K), L2.1
/Power,IO,FETs,Comms/L4_IN: L4.1, L7.2
/Power,IO,FETs,Comms/U3VIN: C20.1, C21.1, C22.1, L2.2, U3.1 (VIN), U3.2 (EN/UVLO)
/Power,IO,FETs,Comms/out0_g: Q1.4 (G), R1.1
/Power,IO,FETs,Comms/out1_g: Q1.1 (G), R3.1
CAN0_RX: U2.4 (RXD); also elsewhere on the board
CAN0_TX: U2.1 (TXD); also elsewhere on the board
CAN_H: JP2.2 (C), L1.2; also elsewhere on the board
CAN_L: JP2.3 (C), L1.3; also elsewhere on the board
GND: C1.2, C2.2, C3.2, C5.1, C15.2, C16.2, C17.2, C19.2, C20.2, C21.2, C23.2, C26.2, C27.2, C28.2, Q1.2 (S), Q1.3 (S), R12.2, R17.2, R19.2, R20.2, R23.2, R37.2, U2.2 (VSS), U2.8 (S), U2.9 (PAD), U3.7 (GND); also elsewhere on the board
IO_0: C28.1, D4.1, R2.1; also elsewhere on the board
IO_0_IN: R2.2, R6.1; also elsewhere on the board
IO_1: C3.1, D4.2, R4.1; also elsewhere on the board
IO_1_IN: R4.2, R7.1; also elsewhere on the board
IO_2: C17.1, D5.2, R5.1; also elsewhere on the board
IO_2_IN: R5.2, R8.1; also elsewhere on the board
unnamed: C5.2, R15.2, R22.1
unnamed: C22.2, R12.1
unnamed: D6.1 (K), R19.1
unnamed: D7.1 (K), R37.1
unnamed: JP2.1 (A), R15.1
unnamed: JP2.4 (B), R22.2
OUT_0: R1.2; also elsewhere on the board
OUT_0_NEG: D1.2 (A), Q1.6 (D); also elsewhere on the board
OUT_1: R3.2; also elsewhere on the board
OUT_1_NEG: D3.2 (A), Q1.5 (D); also elsewhere on the board
VIN_MON: C27.1, R16.2, R17.1; also elsewhere on the board
V_FUSED: C1.1, D1.1 (K), D2.2 (A), D3.1 (K), D6.2 (A), F1.2, R16.1; also elsewhere on the board
V_IN: F1.1; also elsewhere on the board

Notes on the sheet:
RED
OUT 0 MOSFET CONTROL
12-50V Input, 5V 300mA Output PWM Buck Converter
OUT 1 MOSFET CONTROL
VIN Fuse
Inputs
CAN Transceiver
Power LED
Fit with 5A
Blue
5V LED

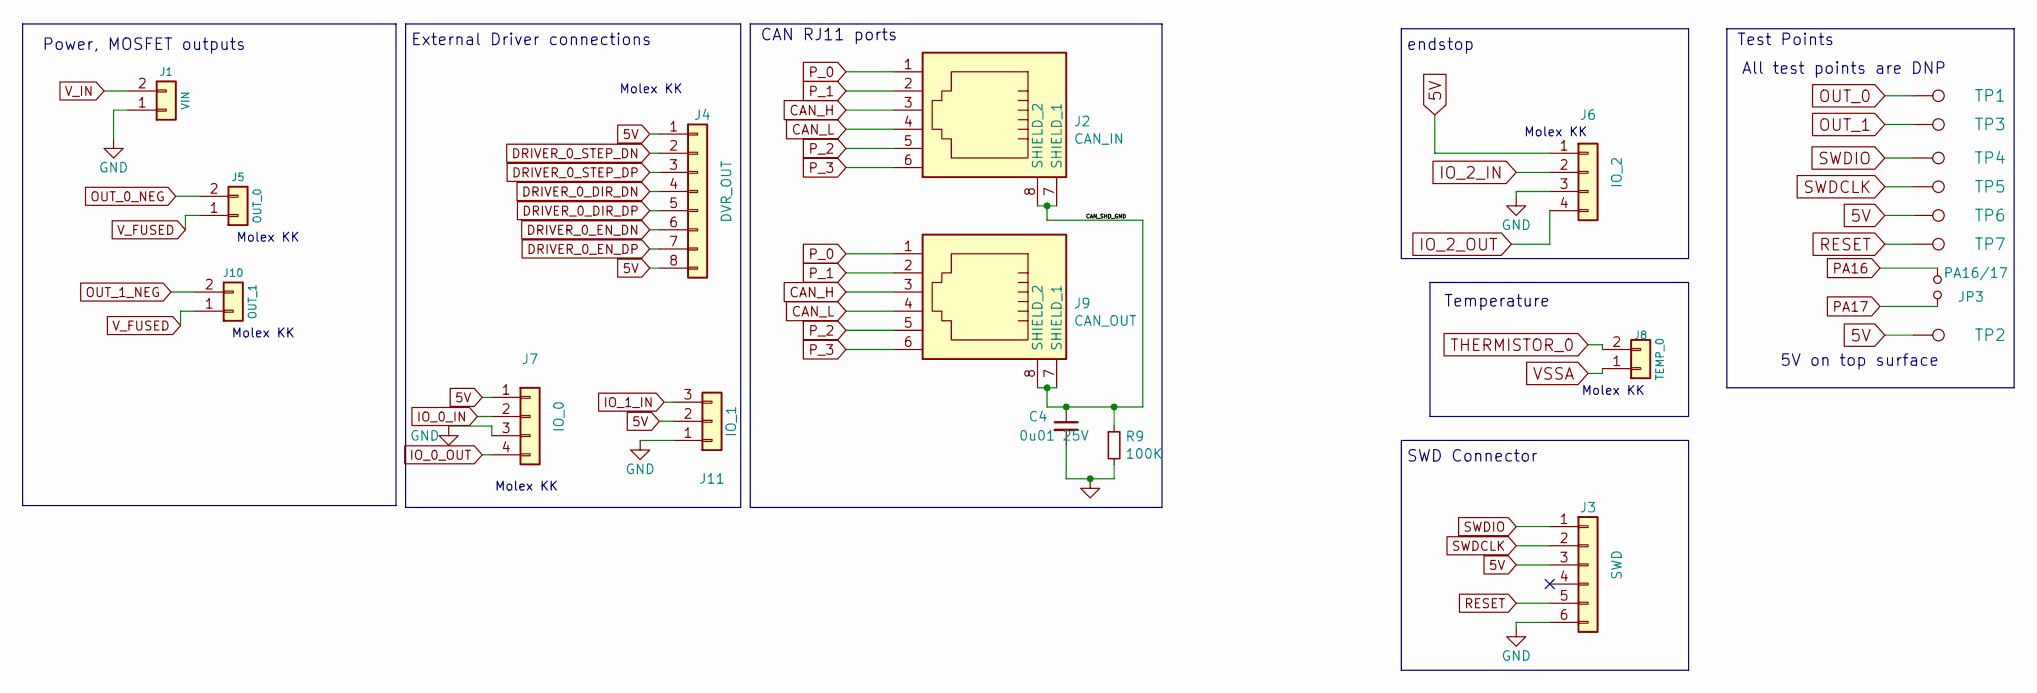
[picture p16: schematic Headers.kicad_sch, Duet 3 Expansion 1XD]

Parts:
C4: 0u01 25V; C_0402_1005Metric_Wbry; Part Number TMK105B7103KV-F
J1: VIN; JST_VH_B2P-VH_1x02_P3.96mm_Vertical; Part Number B2P-VH(LF)(SN)
J2: CAN_IN; RJ11_6P6C_half_shield; Part Number 615006143421
J3: SWD; JST_ZH_1x06_P1.5_B6B-ZR-SM4-TF; Part Number DNP
J4: DVR_OUT; Molex_KK-254_AE-6410-08A_1x08_P2.54mm_Vertical; Part Number 61900811121
J5: OUT_0; Molex_KK-254_AE-6410-02A_1x02_P2.54mm_Vertical; Part Number 61900211121
J6: IO_2; Molex_KK-254_AE-6410-04A_1x04_P2.54mm_Vertical; Part Number 61900411121
J7: IO_0; Molex_KK-254_AE-6410-04A_1x04_P2.54mm_Vertical; Part Number 61900411121
J8: TEMP_0; Molex_KK-254_AE-6410-02A_1x02_P2.54mm_Vertical; Part Number 61900211121
J9: CAN_OUT; RJ11_6P6C_half_shield; Part Number 615006143421
J10: OUT_1; Molex_KK-254_AE-6410-02A_1x02_P2.54mm_Vertical; Part Number 61900211121
J11: IO_1; Molex_KK-254_AE-6410-03A_1x03_P2.54mm_Vertical; Part Number 61900311121
JP3: PA16/17; PinHeader_1x02_P2.54mm_Vertical; Part Number DNP
R9: 100K; R_0402_1005Metric_Wbry; Part Number RK73H1ETTP1003F
TP1: OUT_0; TestPoint_Pad_D2.0mm; Part Number virtual component - DNP
TP2, TP6: 5V; TestPoint_Pad_D2.0mm; Part Number virtual component - DNP
TP3: OUT_1; TestPoint_Pad_D2.0mm; Part Number virtual component - DNP
TP4: SWDIO; TestPoint_Pad_D2.0mm; Part Number virtual component - DNP
TP5: SWDCLK; TestPoint_Pad_D2.0mm; Part Number virtual component - DNP
TP7: RST; TestPoint_Pad_D2.0mm; Part Number virtual component - DNP

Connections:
5V: J3.3, J4.1, J4.8, J6.1, J7.1, J11.2, TP2.1, TP6.1; also elsewhere on the board
/Headers/CAN_SHD_GND: C4.1, J2.7 (SHIELD_1), J2.8 (SHIELD_2), J9.7 (SHIELD_1), J9.8 (SHIELD_2), R9.1
CAN_H: J2.3, J9.3; also elsewhere on the board
CAN_L: J2.4, J9.4; also elsewhere on the board
DRIVER_0_DIR_DN: J4.4; also elsewhere on the board
DRIVER_0_DIR_DP: J4.5; also elsewhere on the board
DRIVER_0_EN_DN: J4.6; also elsewhere on the board
DRIVER_0_EN_DP: J4.7; also elsewhere on the board
DRIVER_0_STEP_DN: J4.2; also elsewhere on the board
DRIVER_0_STEP_DP: J4.3; also elsewhere on the board
GND: C4.2, J1.1, J3.6, J6.3, J7.3, J11.1, R9.2; also elsewhere on the board
IO_0_IN: J7.2; also elsewhere on the board
IO_0_OUT: J7.4; also elsewhere on the board
IO_1_IN: J11.3; also elsewhere on the board
IO_2_IN: J6.2; also elsewhere on the board
IO_2_OUT: J6.4; also elsewhere on the board
OUT_0: TP1.1; also elsewhere on the board
OUT_0_NEG: J5.2; also elsewhere on the board
OUT_1: TP3.1; also elsewhere on the board
OUT_1_NEG: J10.2; also elsewhere on the board
PA16: JP3.2; also elsewhere on the board
PA17: JP3.1; also elsewhere on the board
P_0: J2.1, J9.1
P_1: J2.2, J9.2
P_2: J2.5, J9.5
P_3: J2.6, J9.6
RESET: J3.5, TP7.1; also elsewhere on the board
SWDCLK: J3.2, TP5.1; also elsewhere on the board
SWDIO: J3.1, TP4.1; also elsewhere on the board
THERMISTOR_0: J8.2; also elsewhere on the board
VSSA: J8.1; also elsewhere on the board
V_FUSED: J5.1, J10.1; also elsewhere on the board
V_IN: J1.2; also elsewhere on the board

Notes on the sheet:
Molex KK
Power, MOSFET outputs
CAN RJ11 ports
All test points are DNP
5V on top surface
Test Points
SWD Connector
External Driver connections
Temperature
endstop

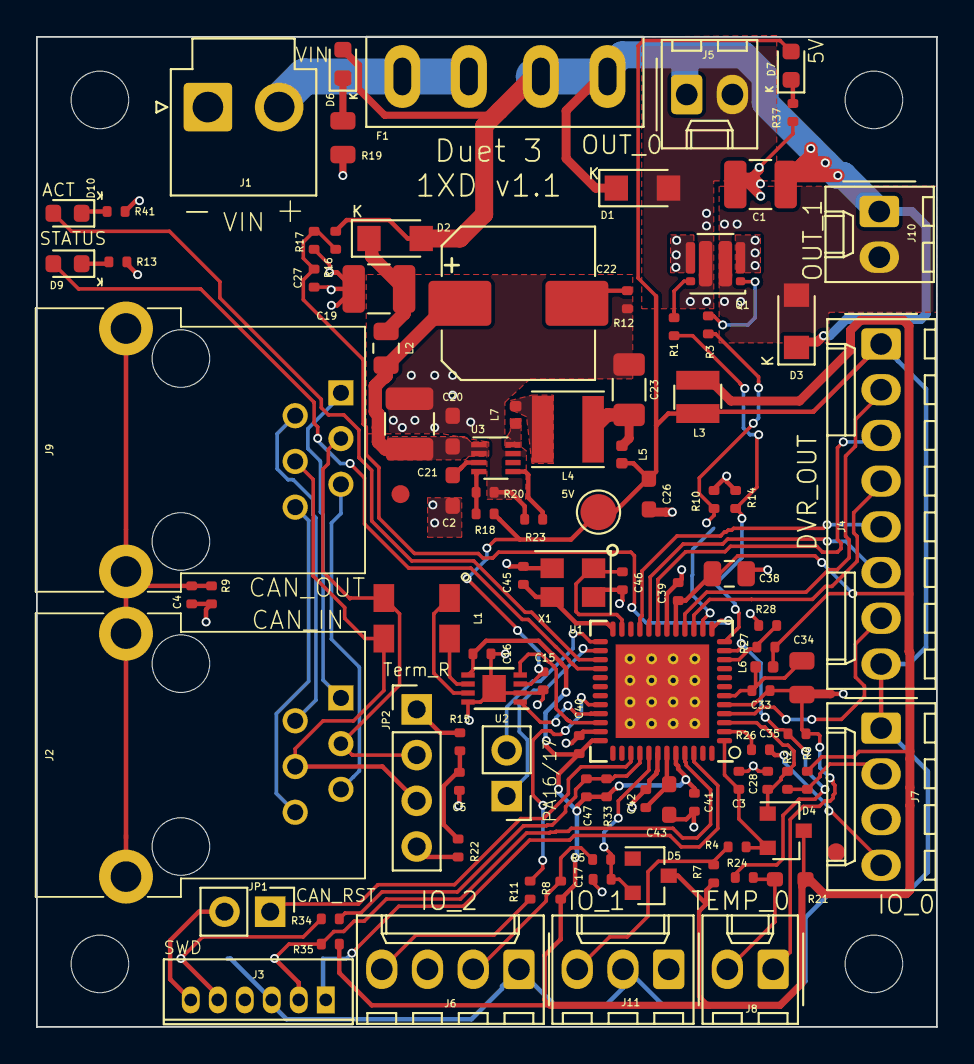
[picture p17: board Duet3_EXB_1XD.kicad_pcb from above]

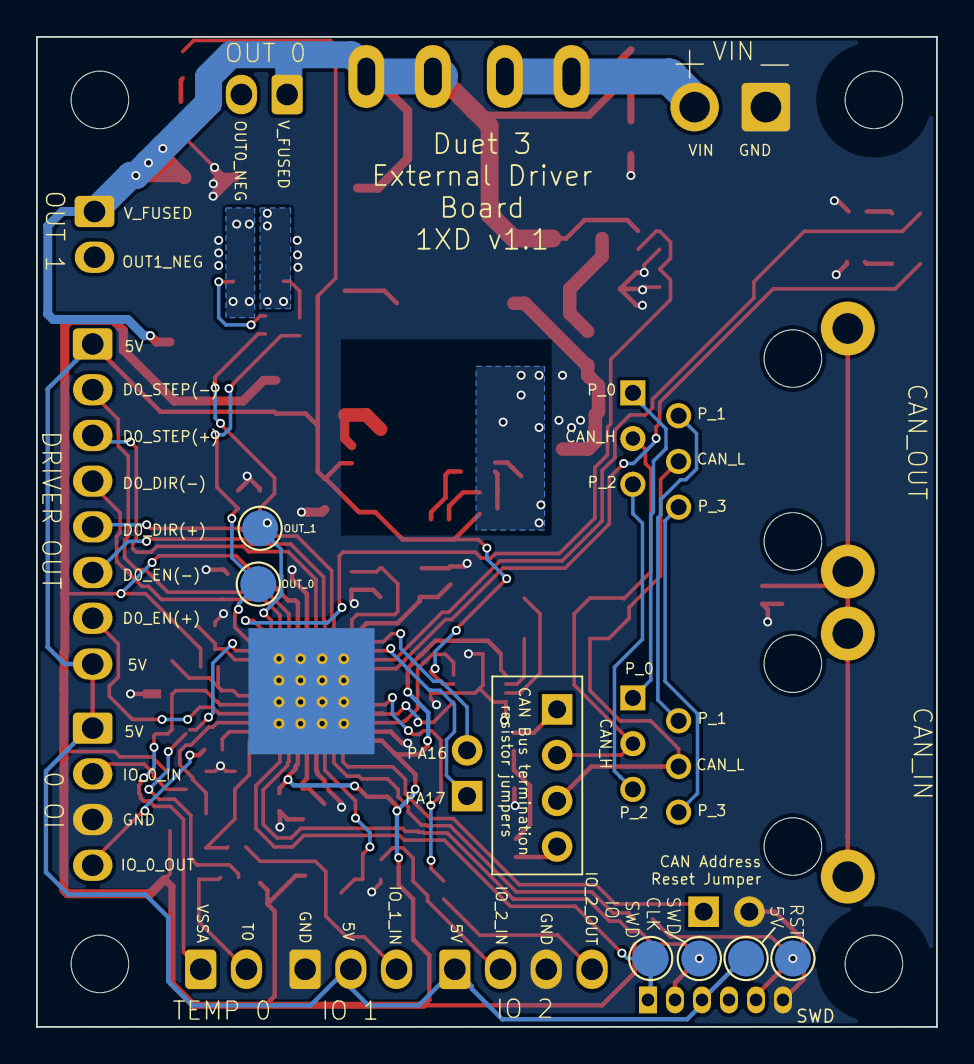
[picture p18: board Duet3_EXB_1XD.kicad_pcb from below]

Board: 2 copper layers, 50.0 x 55.0 mm, 110 parts (6 on the bottom side), 72 nets.

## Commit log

2020-06-15 Schematic, STEP and documentation images
2020-06-22 Added the iBOM for the 1XD board
2023-11-13 v1.1 Source files
    [Duet3_EXB_1XD.kicad_pcb, Duet3_EXB_1XD.kicad_sch, Headers.kicad_sch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]
